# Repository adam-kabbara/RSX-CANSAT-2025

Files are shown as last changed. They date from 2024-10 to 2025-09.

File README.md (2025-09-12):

# RSX CanSat 2T4-2T5 Designs 

<div style="display: flex; gap: 20px; align-items: center;">
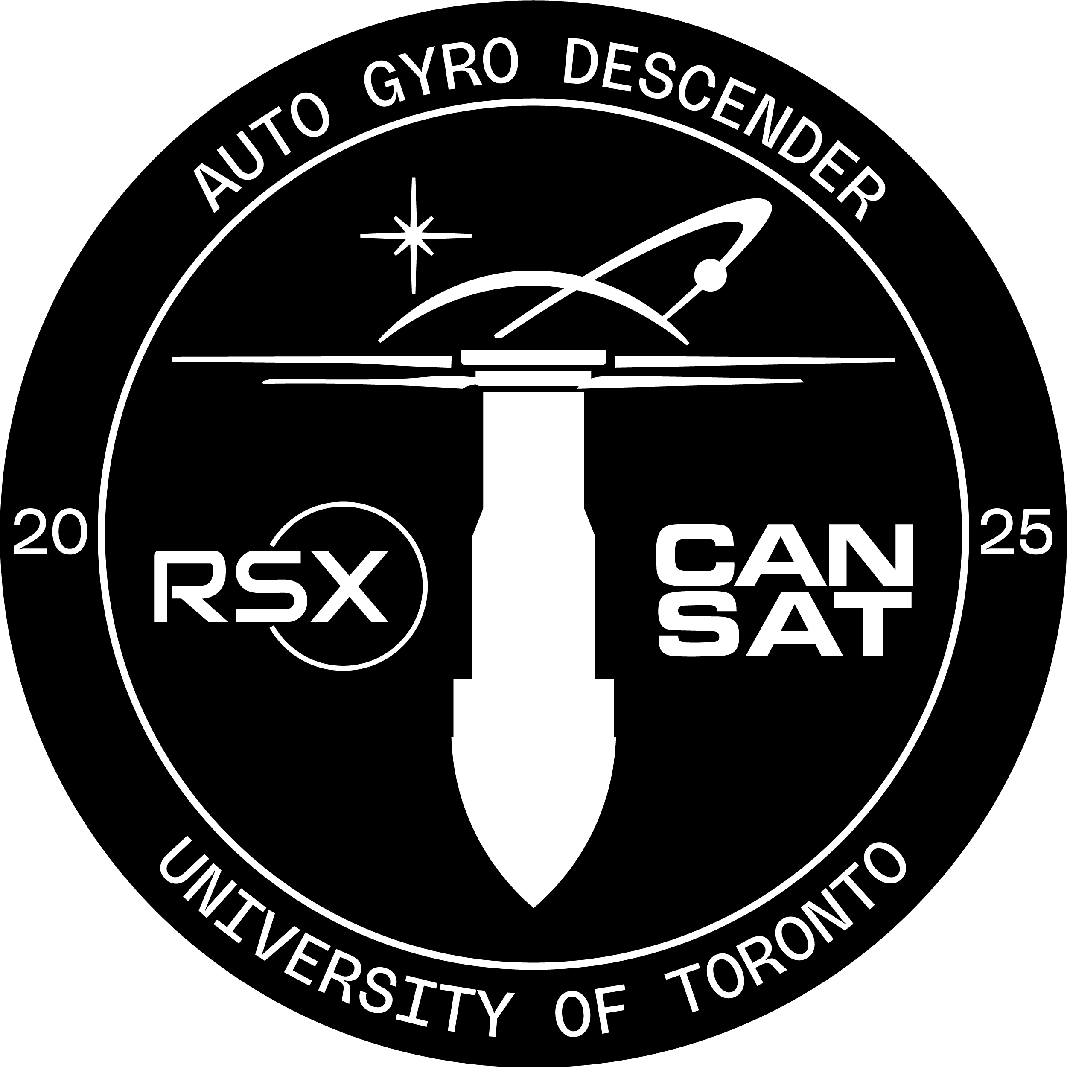
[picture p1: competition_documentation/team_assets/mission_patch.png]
mission_patch
  
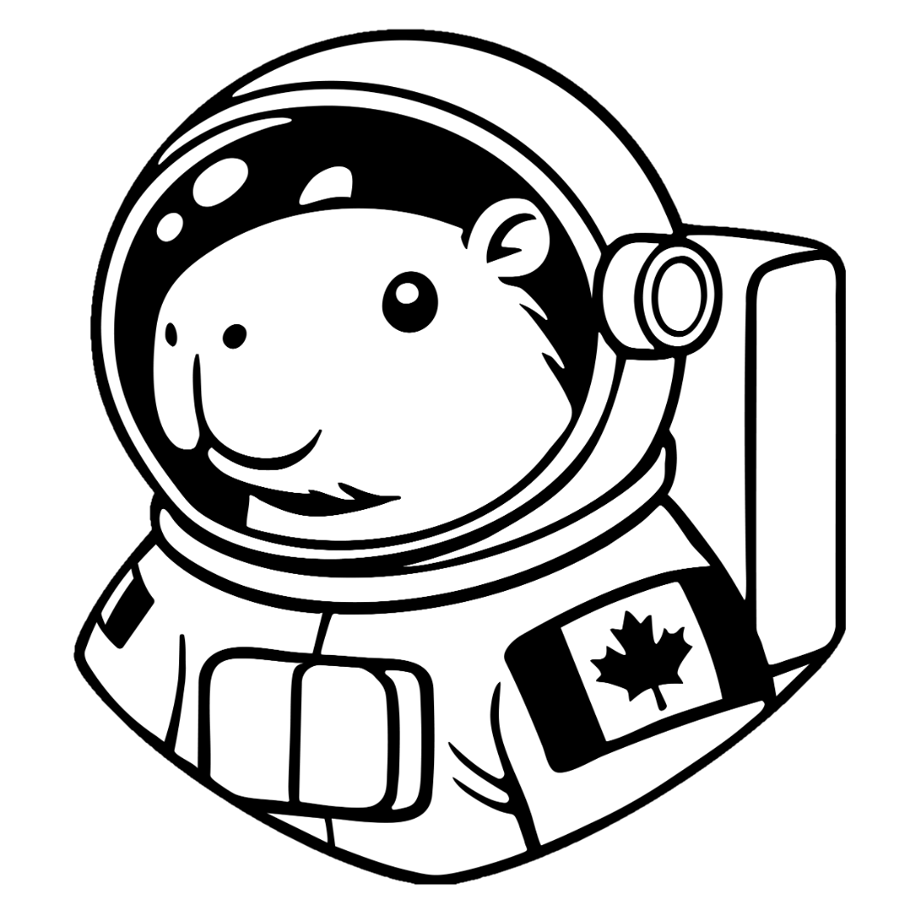
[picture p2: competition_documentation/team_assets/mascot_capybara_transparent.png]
mascot_capybara
  
  uoft_engineering_logo
</div>
<br>

This repository is designed to manage the files made by the CanSat Team under the Robotics for Space eXploration (RSX) design team at the University of Toronto. 

**Competition Team Members:**
- Adam Kabbara | CanSat Team Lead
- Arthur Goetzke-Coburn | Mechanical Team Lead
- Daniel Yu | Electrical Team Lead
- Luke Watson | Software Team Lead
- Gianluca Ceccacci | Mechanical Team Member
- Nour Barsoum | Electrical Team Member
- Angelique Liao | Software Team Member
- Alexey Albert | Mechanical Team Member
- Robert Saab | Electrical Team Member

**CanSat Competition:**
- 📅 June 5-8, 2025
- 📍 Monterey, Virginia, United States
- 📃 [Mission document](CanSat_Mission_Guide_2025e.pdf)

**Competition Deliverables:**
- 🏆 95.87725%: [CanSat 2025 Winners](https://cansatcompetition.com/winners.html)
- 📋 Scoresheet: [TBA]()
- 💾 Mission Data: [Team #3114 Mission Data](competition_documentation/3114_mission_data_cansat_2025.csv.xlsx)
- 📝 Preliminary Design Review: [Team #3114 PDR](competition_documentation/deliverables/Cansat2025_3114_PDR.pdf)
- 🛠️ Critical Design Review: [Team #3114 CDR](competition_documentation/deliverables/Cansat2025_3114_CDR.pdf)
- 🌡️ Environemental Testing Document: [Team #3114 ENV](competition_documentation/deliverables/Cansat2025_3114_Mission_Operations_Manual.pdf)
- 🗂️ Mission Operations Manual: [Team #3114 MOM](competition_documentation/deliverables/Cansat2025_3114_Mission_Operations_Manual.pdf)
- 🛰️ Post Flight Review: [Team #3114 PFR](competition_documentation/deliverables/Cansat2025_3114_PFR.pdf)
- Note: The links above may be outdated.

**Competition Results:**
- 🗺️ 5th Place Internationally!
- 🌎 1st in North America!
- 🍁 1st in Canada!

## Folder Organization

**Calculations:**
<br> Python functions and calculations for sizing inductors and capacitors in a power electronics circuit, including formulas for inductor DC current, ripple current, peak current, and minimum capacitor value, with example calculations and printouts.

**Circuit Design:**
<br>This folder contains all the KiCad printed circuit board (PCB) designs our team has created. It also includes each PCB's related schematic, layout, and gerber files with associated custom KiCad symbols, footprints, and 3D models.

**Competition Documention:**
<br>All deliverables, team logos, and full results from the 2025 CanSat Competition in Monterey, Virginia, USA!

**Full Sensor Setup:**
<br>Initial code used to connect all payload sensor electronics together for testing before integration with full software telemetry.

**Ground Station/Telemetry Source:**
<br>Mission specific operations on payload and ground station.

**PID:**
<br>The code, notebooks, and scripts for developing, testing, and simulating PID control algorithms and sensor integration for the CanSat project.

**PFR Plots:**
<br>Contains Python scripts and output images for generating 2D and 3D plots of CanSat mission and sensor data, including GPS, altitude, and other telemetry visualizations for post-flight review and analysis.

**Sensor Testing:**
<br>All sensors used on our CanSat are tested separately using an ESP32-WROOM-32D Dev Module microcontroller. This folder contains all related information regarding the tests completed on these sensors including past designs, schematics, pin connections, and code.

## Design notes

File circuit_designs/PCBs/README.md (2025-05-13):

# 2025_Competition_Boards
This folder contains a snapshot of all the schematics, boards, and gerber files of the boards taken to the 2025 CanSat Competition.

# Final_Versions
This folder contains the entire KiCad PCB projects of all three boards inclduing improvements made after competition.

# Old_Versions
This folder contains the entire KiCad PCB projects all three boards before technical review. Most of the stitched VIAs are incorrect.

# Power_Management_Prototypes
This folder contains the KiCad projects of initial buzzer and power management board designs. All were later combined into the CanSat_Power_Management_Board.

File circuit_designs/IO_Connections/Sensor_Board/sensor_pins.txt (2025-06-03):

CanSat_Sensor_Board Pin Connections

Format: <Sensor Connection> --> <ESP32 Pins>

SparkFun XBee Explorer (XBee Pro SB3):
DIN     --> GPIO17
DOUT    --> GPIO16
3.3V    --> 3.3V (Power Board)
GND     --> GND

Hall Effect Sensor:
Vout    --> GPIO34
GND     --> GND
VCC     --> 3.3V (Power Board)

Adafruit BME280 (Temp & Pressure):
VIN --> 3.3V (Power Board)
GND --> GND
SCK --> GPIO22
SDI --> GPIO21

BN-220 (GPS):
GND         --> GND
TX (White)  --> RXD1/GPIO9
RX (Green)  --> TXD1/GPIO10
VCC         --> 3.3V (Power Board)

Adafruit LIS3MDL (Magnetometer):
SDA --> GPIO21
SCL --> GPIO22
GND --> GND
VIN --> 3.3V (Power Board)

Adafruit BNO085 (IMU):
VIN --> 3.3V (Power Board)
RST --> GPIO5
CS  --> GPIO15
DI  --> GPIO23
SCL --> GPIO18
SDA --> GPIO19
INT --> GPIO35 & 10k Ohm Pull-Up Resistor --> 3.3V (Power Board)
P0  --> 3.3V (Power Board)
P1  --> 3.3V (Power Board)
GND --> GND

LED (Power Indicator):
(+) --> 10 Ohm Resistor --> 3.3V (Power Board)
(-) --> GND

Servo 1 (Fin 1):
Signal  --> GPIO2
VCC     --> 7.4V (Power Board)
GND     --> GND

Servo 2 (Fin 2):
Signal  --> GPIO4
VCC     --> 7.4V (Power Board)
GND     --> GND

Servo 3 (Camera):
Signal  --> GPIO27
VCC     --> 7.4V (Power Board)
GND     --> GND

Servo 4 (CPL 1):
Signal  --> GPIO14
VCC     --> 7.4V (Power Board)
GND     --> GND

Servo 5 (CPL 2):
Signal  --> GPIO12
VCC     --> 7.4V (Power Board)
GND     --> GND

Servo 6 (CPL 3):
Signal  --> GPIO13
VCC     --> 7.4V (Power Board)
GND     --> GND

Camera Board (JST):
VCC     --> 7.4V (Power Board)
Signal1 --> GPIO32
Signal2 --> GPIO33
Data1   --> GPIO25
Data2   --> GPIO26
GND     --> GND

Power Board (JST):
3.3V
7.4V    --> 5V & Six Servos & Camera Board (JST)
ADC     --> GPIO39
GND

Booster + Battery connections not included here, as well as various resistors and capacitors, please see the schematic for more details here:
/$USER/RSX-CANSAT-2T4-2T5/RSX-CANSAT-2025/circuit_designs/PCBs/CanSat_Sensor_Board/CanSat_Sensor_Board.kicad_sch

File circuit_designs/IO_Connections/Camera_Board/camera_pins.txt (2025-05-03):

CanSat_Camera_Board Pin Connections

Format: <JST Connection> --> <ESP32 Camera Pins>

Acronyms:
PRC = Payload Release Camera (Camera 1)
GC  = Ground Camera (Camera 2)

JST Connection: 
VCC     --> PRC 5V & GC 5V
Signal1 --> PRC GPIO14
Signal2 --> GC GPIO14
Data1   --> PRC GPIO21
Data2   --> GC GPIO21
GND     --> PRC GND & GC GND

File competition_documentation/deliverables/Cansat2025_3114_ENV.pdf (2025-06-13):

### Team Logo Here (If You Want)

# Environmental Test Document

# Team #3114 Robotics for Space eXploration (RSX)

### Here

### (If You Want) Overview

# - Thermal test - Vibration test - Vaccuum test - Drop test

# Even though the vacuumed test was not able to reach the expected apogee of 700m, changing the code to allow apogee to be reached around the maximum vacuumed (~200 m) still displayed how the cansat would eject once it reaches apogee

### Here

# (If You Want) Drop Test Configuration

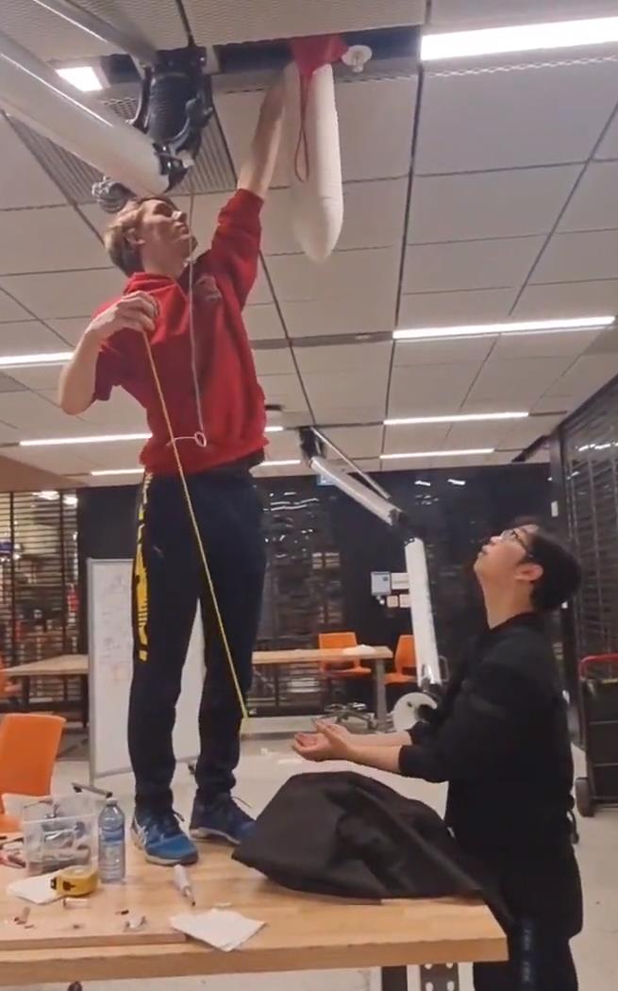
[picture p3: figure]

### Requirements:

### Telemetry must be

received before, during,
and after the drop test.

### Power must not be lost

upon dropping the system.

### Physical components must not detach upon dropping

the CanSat.

### Components of the CanSat should not be damaged from the drop

test.

### The test structure must not

be held by hand.

### Materials:

### 61 cm, 5/8" tubular nylon cord

### Eyebolt

### Scrap wood and Clamps

### Winter Jackets (padding)

Setup:

Two 2x4s are placed on the corner of the balcony above Myhal Arena and a large piece of scrap plywood with an eyebolt screwed into the centre and directed towards the ground is placed on top of the 2x4s. The wood is clamped to the rails of the balcony using 4 clamps. The eyebolt of the testing rig is attached via the nylon cord to a second eyebolt screwed into a plywood disk fed through the hole of the parachute and taped to the parachute to ensure it stays centered. Place winter jackets on the ground below the test fixture to act as a safety net for the CanSat if it drops.

### Here

# (If You Want) Drop Test Procedures

## Procedure:

1) Power on CanSat.
2) Verify telemetry is being received.

## 3) Assemble the testing rig described in the previous

slide.

4) Start video recording this testing procedure.

## 5) Feed the wooden disk with an eyebolt through the

## hole of the parachute. Use tape to keep the eyebolt

in the centre of the hole.

6) Using the tubular nylon, attach these two eyebolts,

a distance of 61cm away from each other.

## 7) Photograph how the CanSat and parachute are

fastened to the testing rig.

## 8) Raise CanSat by the attached cord, so that the

## attachment points of the cord, on the eye bolt and the

parachute, are at the same height.

9) Photograph the CanSat at this point in the procedure.
10) Release the CanSat.
11) Photograph the CanSat after the drop.
12) Verify the CanSat did not lose power.
13) Turn the CanSat off.
14) Inspect for any damage, or detached parts.
15) Verify telemetry is still being received.
16) Stop the video recording.

## 17) Make this video available to the judges and ensure it

does not exceed 5 minutes in length.

### Here

# (If You Want) Drop Test Results

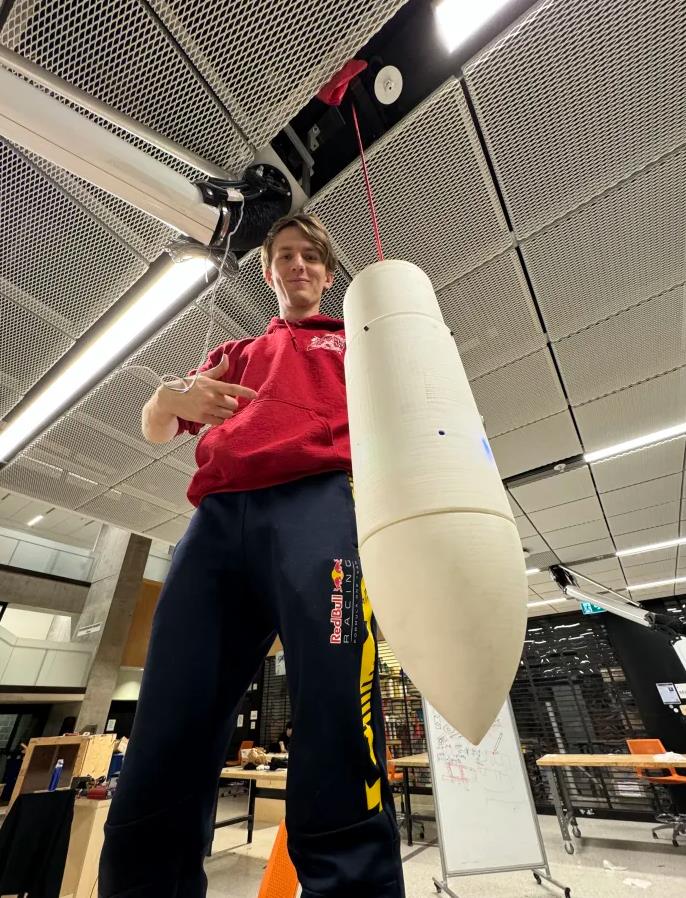
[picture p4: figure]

# Video Link: https://drive.google.com/file/d/1sROrkcR7NDwY3

mso1kv6UxrnZrP9bl7X/view?usp=sharing (https://drive.google.com/file/d/1sROrkcR7NDwY3mso1kv6UxrnZrP9bl7X/view?usp=sharing)

# Result: The cansat was still functioning normally

after the drop test, and it was structurally sound,

# as explain by our mech lead, Arthur in the linked

video.

### Here

# (If You Want) Thermal Test Configuration

### Requirements:

Power must not be lost while heating the system.

### Components of the CanSat should not be damaged from the Thermal

test.

### The rubber bands applying the force to lift the rotor joints shall take the same amount of time to deploy the rotors before and after the thermal

test.

### Materials:

### Thermal Chainber (3D printer with heated bed)

### Heat Gun

### LCD thermometer

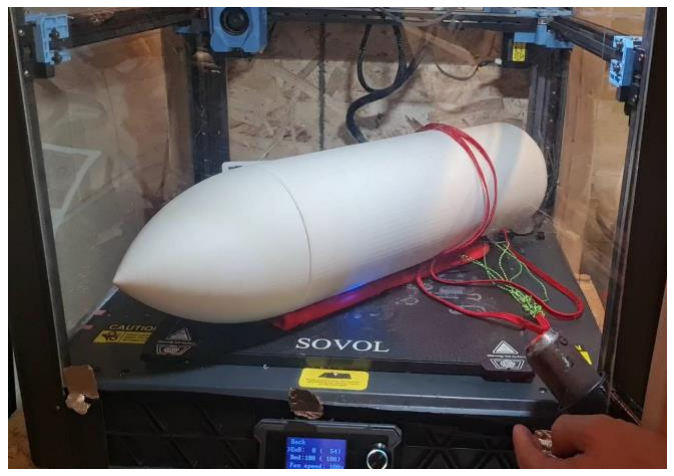
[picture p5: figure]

Setup:

Set up the heated but to 100 degrees C. This makes the thermal chamber reach 60 degrees C. The thermal chamber loses heat due to imperfections in the chamber. We use

Before putting the cansat in the chamber, put a thermally insulating layer to avoid the cansat direct contact with the 100-degree bed.

### Here

# (If You Want) Thermal Test Procedures

Procedure:

1) Using a Newton Force Meter Spring Scale,

measure the force required to lift a single air

foil. Video this process.

2) Clamp one end of the fin down along a

distance of 2cms down the fin. Place the mass

at the opposite end, and using two rulers,

measure the8) Raise CanSat by the attached

cord, so that the attachment points of the cord,

on the eye bolt and the parachute, are at the

same height. distance that the system bends

downward. Video tape this process.

3) Place CanSat into a thermal chamber in a

secure fashion and video this process.

4) Photograph the manner in which the CanSat

is secured.

5) Turn on the CanSat.
6) Close and seal the thermal chamber.
7) Turn on the heat source.
8) Monitor the temperature and turn off the heat

source when the internal temperature reaches

60C and turn on the heat source when the

temperature drops to 55C.

9) Take a short video highlighting abidence to

the above step.

10) Maintain the test conditions for two hours.
11) Turn off the heat source and perform visual

inspection and any functional tests to verify the

Cansat survived the thermal exposure and can

operate as expected. Ensure there is no visible

warping or any broken or loose components.

12) Photograph the system.
13) Start a video recording.
14) With the CanSat still hot, remove the

CanSat from the chamber.

15) Test any mechanisms and structures to

ensure the integrity has not been compromised.

Force deployment and ensure the AGDS does

not get stuck within the CC due to thermal

expansion.

16) Verify through telemetry that the electronics

are consistently functional.

17) Turn off the CanSat.
18) Verify epoxy joints and composite materials

still maintain their strengths by repeating steps

1) and 2).
19) Stop the video recording
20) Splice together the many short videos into

one long video. Ensure this video is less than 5

minutes long.

21) Make this video available to the judges.

### Here

# (If You Want) Thermal Test Procedures

Procedure:

1) Test the CanSat motor release system is

valid. Video tape this process.

2) Place a thermometer inside of the thermal

chamber. Place a glove on the layer of the

thermal chamber avoid CanSat's direct

attachment to the heat bed. Video tape this

process.

3) Place CanSat into a thermal chamber in a

secure fashion and video this process.

4) Photograph the manner in which the CanSat

is secured.

5) Tap the sides of the thermal chamber

container and make sure it is properly sealed.

6) Double check if the thermal chamber is

properly sealed.

7) Turn on the heat source.
8) Monitor the temperature and turn off the heat

source when the internal temperature reaches

60C and turn on the heat source when the

temperature drops to 55C.

9) Take a short video highlighting abidence to

the above step.

10) Maintain the test conditions for two hours.
11) Turn off the heat source and perform visual

inspection and any functional tests to verify the

Cansat survived the thermal exposure and can

operate as expected. Ensure there is no visible

warping or any broken or loose components.

12) Photograph the system.
13) Start a video recording.
14) With the CanSat still hot, remove the

CanSat from the chamber.

15) Test any mechanisms and structures to

ensure the integrity has not been compromised.

Force deployment and ensure the AGDS does

not get stuck within the CC due to thermal

expansion.

16) Verify through telemetry that the electronics

are consistently functional.

17) Turn off the CanSat.
18) Verify epoxy joints and composite materials

still maintain their strengths by repeating steps

### Here

# (If You Want) Thermal Test Results

# Video link: https://drive.google.com/file/d/1xN-CH3U1Kcelx69eaLlpqZKlPzbh1Y-

5/view?usp=drive_link (https://drive.google.com/file/d/1xN-CH3U1Kcelx69eaLlpqZKlPzbh1Y-5/view?usp=drive_link)

# Result shows that the rotor deployment has not been affected by high

temperature around 60 degrees.

### Here

# (If You Want) Vibration Test Configuration

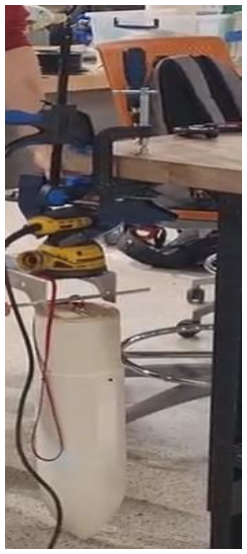
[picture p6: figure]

### Requirements:

### Accelerometer data must continue to be recorded and sent throughout the

entirety of the testing procedure.

### The CanSat must be able to withstand the vibrational shock without physical

damage.

### The Random Orbital Sander must not

be held by hand.

Materials:

Random Orbital Sander (GIVE MODEL NUMBER)

Bench Vise

Plywood, Metal Brackets, Screws to fasten, Bolt, Washer, and Nut

Double sided Tape

Setup:

The orbital sander will be secured, downward facing, in the vise bench. A plywood disk the size of the sander's face will be attached using strong double-sided tape to the sander itself. This disk will have two small metal brackets screwed into it, spaced the width of the CC's eyebolt, enabling a bolt to pass through them and the eye bolt of the CC. A washer and nut will be tightened, creating pressure between the two brackets and the eyebolt.

### Here

# (If You Want) Vibration Test Procedures

## Procedure:

1) Power on the CanSat.
2) Verify accelerometer data is being collected.

### 3) Take a photograph of this setup. Take additional

### photos highlighting how the CanSat was secured

explained in the setup on the previous slide.

4) Start a video recording.
5) Power up the sander.

### 6) Once the sander is up to full speed, wait 5

seconds.

7) Power down the sander to a full stop.
8) Repeat steps 5) to 7) four more times.
9) Photograph the CanSat.
10) Inspect the CanSat for damage and functionality.
11) Verify accelerometer data is still being collected.

### 12) Stop the video recording and ensure it is under 5

### minutes in length. Make this video available to the

judges.

13) Power down CanSat.

### Here

# (If You Want) Vibration Test Results

# - Results show that the cansat is still function and transmitting data after being

subjected to 20 to 29 G of vibrations.

# - Video Link: https://drive.google.com/file/d/1s6XSHnLbIq4v2N4K2l2q6ZPo6ZZZhTwv/view

?usp=drive_link (https://drive.google.com/file/d/1s6XSHnLbIq4v2N4K2l2q6ZPo6ZZZhTwv/view?usp=drive_link)

- Note: The magnetometer readings are showing 0 Gauss due to the small magnetic fields likely

## in the decimals and our GUI does not specify further than one full unit

- Note: The accelerometer readings are only showing up to +-4G due to the original settings of the BNO-085 IMU sensor, however, our orbital saner is creating up to +-25G.

### Here

# (If You Want) Vacuum Test Configuration

### Requirements:

Telemetry must be received before, during, and after the vacuum test.

Telemetry must be exportable as a .csv.

### The CanSat must decouple based off the simulated altitude data at 75%

of the simulated apogee.

### Materials: IKEA 12-gallon bin

### Vacuum

### Gray Duct Tape

### Clear garbage bag

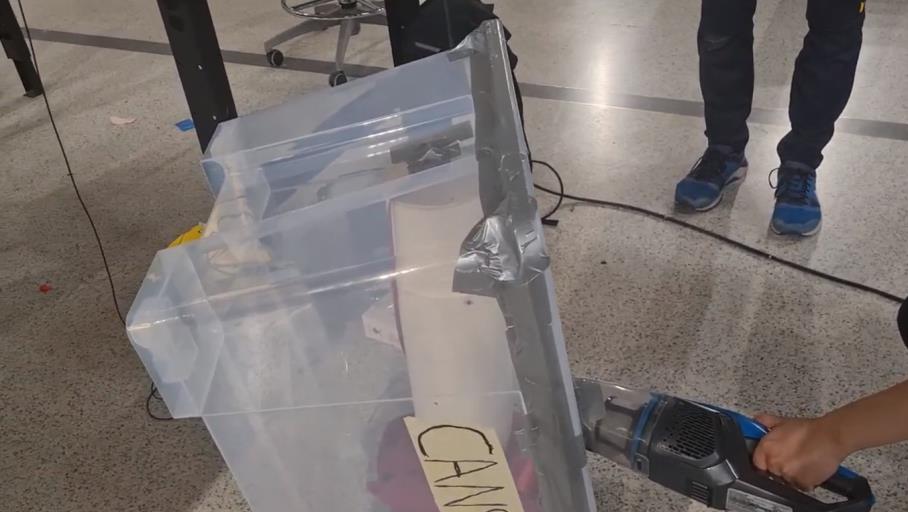
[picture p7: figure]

Setup:

Using the CanSat Container's eyebolt, the system is to be taped to the bin. A towel is placed below the suspended system for padding. A garbage bag was pulled tight over the open side of the bin where the lid would go, and the bag is taped to the bin using the sealant tape. A small hole is cut into the bag and it is pulled over the nozzle of the vacuum. The edges of this tear are taped to the vacuum in order to create an airtight chamber.

### Here

# (If You Want) Vacuum Test Procedures

## Procedure:

1) Start a video recording.

### 2) Suspend the fully configured and powered CanSat in

### the vacuum chamber in the manner described in the

setup on the previous slide.

3) Take a photograph of this setup.
4) Turn on the vacuum to start generating suction.

### 5) Monitor the telemetry in simulation mode and stop the

vacuum when the peak altitude has been reached.

### 6) Let the air enter the vacuum chamber slowly and

### monitor the operation of the CanSat. The air will leak

through the vacuum cleaner when off.

### 7) Ensure the AGDS decouples from the CC at 75%

apogee.

### 8) Stop the video and ensure it shows all mechanisms

activated based on altitude changes.

9) Collect the CanSat from the vacuum chamber.
10) Collect and save the telemetry.
11) Power off the CanSat.

### 12) Make the saved telemetry available for the judges to

review.

### 13) Ensure the video is under 5 minutes long and make

it available to the judges.

### Here

# (If You Want) Vacuum Test Results

# - Video link: https://drive.google.com/file/d/1sOdRuyu7-

IHa7KviOOJac89K6n2n80d5/view?usp=sharing (https://drive.google.com/file/d/1sOdRuyu7-IHa7KviOOJac89K6n2n80d5/view?usp=sharing%E2%80%83)

# - The vacuum test was a success even though the pressure in the enclosure did not reach the expected apogee pressure – the finite state machine was able to be performed as the "Apogee" state was reached when the pressure

became constant for a few seconds after rising over a specific threshold.

### Here

### (If You Want) Summary

# - The tests were a success - For next year, it would be nice to have a more powerful vacuume that allows us to simulate lower pressures similar to that which the cansat will experience at apogee (~700)

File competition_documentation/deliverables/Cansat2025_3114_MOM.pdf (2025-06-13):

# Mission Operations Manual (Check List) Team 3114 (RSX) Version 2.0

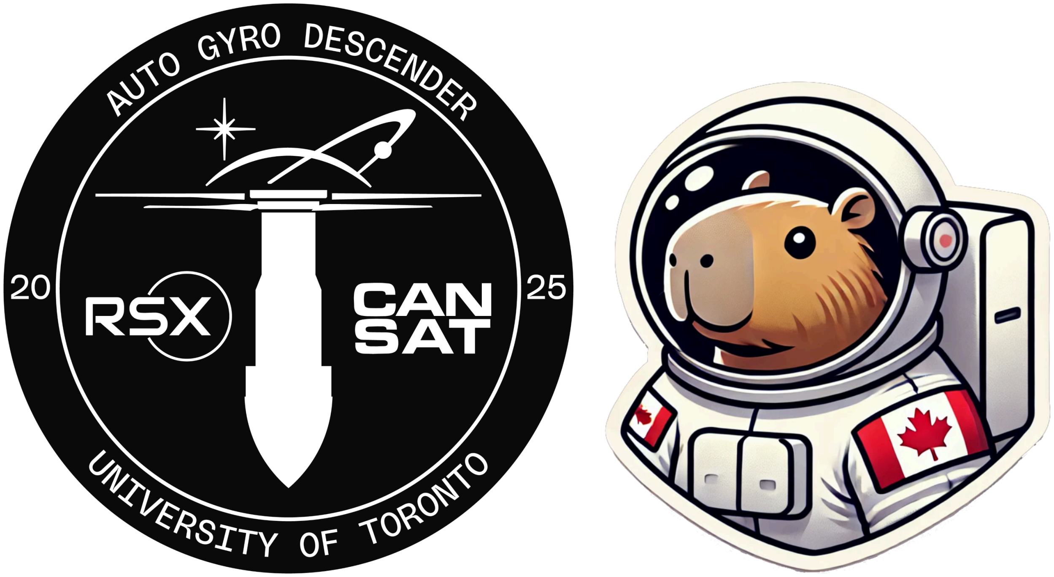
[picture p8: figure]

Ground Station Configuration | 2
Cansat Preparation | 3
Cansat Integration | 4
Launch Preparation | 4
Launch Procedures | 4

Ground Station Configuration
Ground Station Crew (GSC): Luke Watson and Angelique Liao

Ground station crew heads to ground station tables to set up the ground station.
Connect the RPSMA wire from the QHA antenna into the ground station XBee.
Insert the ground station XBee into the SparkFun XBee regulated dongle and connect to the ground station laptop to provide power through the USB port of the ground station laptop.
Place the antenna on the table using the stand and prepare for use as a handheld antenna right before launch.
Turn on the ground station laptop, run the ground station GUI, and select the correct serial (COM) XBee under the connection tab.
Ensure that the Net ID on the XBee is set to the Team ID and change if necessary.
After the Cansat is powered on, check the connection with the ground station under the connection tab to ensure everything is set up correctly. From the GUI, send the altitude calibration command to zero the barometer. Also ensure to set the time as well to either GPS time or ground station computer time depending on the judges’ input. Verify updated values in the telemetry Live Values section.
Finally, to start the mission and telemetry graphing, click Start Mission under the Telemetry tab.

Cansat Preparation
CanSat Crew (CCR): Arthur Goetkze-Coburn, Alexey Albert, Daniel Yu

On the Cansat Payload, open one half of the shroud to verify both Cansat batteries (main and buzzer) are fully charged (~8.4v and 4.2v respectively) and securely connected. Double check the RTC backup battery voltage as well and replace it if the voltage is lower than 3v.
Disconnect the main board from both the power and camera board. Upload the last stable version of the flight software to the main ESP32. Ensure both camera ESP32s have SD cards. Blue SD card belongs to camera 1 (ESP32 closer to JST) and red SD card belongs to camera 2. To access SD card on camera 2, undo the camera cable extension. Reconnect all three boards together, turn on both main and buzzer switches, and ensure that all three boards all light up.
Confirm that the ground station GUI is able to receive telemetry data and is able to detect the ground camera boards after the completion of the Ground Station Configuration operation.
Debug any problems that arise, then put the second half of the shroud back onto the Cansat Payload.
Ensure all the rubber bands on the rotors are attached correctly and replace them if they are broken.
Actuate all four rotors. Both GYRO servos should be at rest (parallel to the shroud direction) at 90 degrees. The Camera servo should also be at rest at 90 degrees (pointing in the normal direction of the Cansat shroud). The rest position of the Release servo is at 0 degrees (holding the payload) Actuate both GYRO servos to 135 (+45 rel) and 45 (-45 rel) Actuate the Camera servo to 100 (+10 rel) and 80 (-10 rel)
Actuate the Release servo to 35 (+35 from rel) and back to 0.
Turn off the Cansat.
Separate the Cansat container from its shoulder. Fold the rotors down and place the Cansat payload into the Cansat container’s wall.
Slide the top rotor shaft into the container's shoulder
Turn the ESP32 back on, this will initiate the container integration sequence which will move the release servo out of the way, allowing the payload’s rotor shaft to slide in, and then actuates 10 seconds later to lock the payload in place.
Turn off the Cansat to save battery and wait for the Integration step.

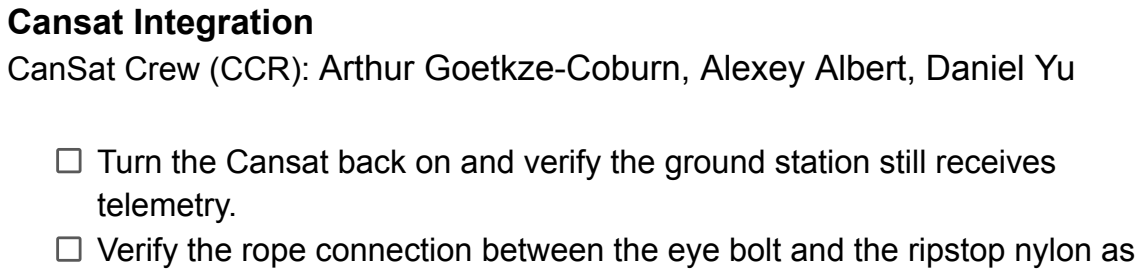
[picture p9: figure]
Cansat Integration; telemetry.

CanSat Crew (CCR): Arthur Goetkze-Coburn, Alexey Albert, Daniel Yu

Turn the Cansat back on and verify the ground station still receives

Verify the rope connection between the eye bolt and the ripstop nylon as well as the connection between the ripstop nylon rope and the 6 parachute ropes.
Fold the parachute and put it in the rocket payload section before the Cansat. Insert the Cansat container into the rocket payload section with the eyebolt going in first and the nose cone pointing to the sky.

Launch Preparation

Take the rocket to the flight line and get a launch pad assignment (should be pad #3 if no changes have been made according to the preflight brief). Walk out with the pad manager and have the rocket installed on the rail. Pad manager installs igniter.
Pad manager verifies igniter continuity if launcher has continuity tester. Team takes a picture next to the rocket.
Team goes back to the flight line and is assigned crew positions.

Launch Procedures
Mission control officer will step through this procedure to launch the Cansat. At any time during the launch procedure, any crew member or officer can call out for a hold to stop the launch. It is required to say HOLD three times using a voice radio to stop the launch. If the hold does not require the rocket to be removed from the launch pad, then the procedures are stopped at the current step. If the hold requires the Cansat to be removed, the removal procedures must be executed.

Flight coordinator will query field judges and spotters if they are ready for the next launch.
Mission Control Officer (Adam) performs any pre-launch checks.
The Mission Control Officer (Adam) will verify with the ground station that the ground station is ready for launch.

Mission Control Officer (Adam) will request Launch Control Officer to select appropriate launch pad.
The Mission Control Officer (Adam) will tell the Launch Control Officer when to launch the rocket.
The Launch Control Officer will launch the rocket.

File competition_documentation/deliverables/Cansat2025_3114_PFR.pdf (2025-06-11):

CanSat 2025 PFR: Team #3114 | RSX | 1

# CanSat 2025 Post Flight Review (PFR) Outline

## Team #3114 Robotics for Space eXploration (UofT)

## Presentation Outline

Presenter: Adam Kabbara

Section | Presenter | Slides
Systems Overview | Arthur Goetzke-Coburn, Gianluca Ceccaci | 4-7
Concept of Operations and Sequence of Events | Alexey Albert, Angelique Liao | 8-11
Flight Data Analysis | Luke Watson, Daniel Yu, Alexey Albert | 12-26
Failure Analysis | Adam Kabbara | 27-29
Lessons Learned | Arthur Goetzke-Coburn, Gianluca Ceccacci | 30-31
Conclusion | Adam Kabbara | 32

## Team Organization

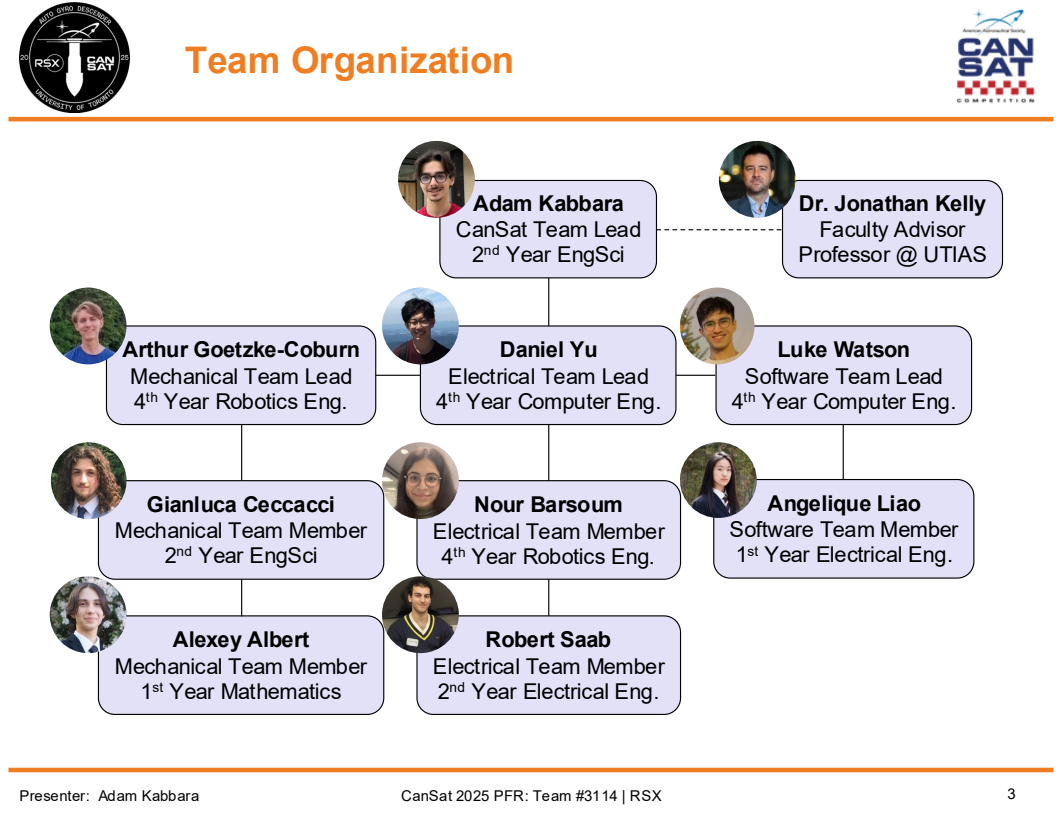
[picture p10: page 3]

Adam Kabbara
CanSat Team Lead
nd Year EngSci

Dr. Jonathan Kelly
Faculty Advisor
Professor @ UTIAS

Arthur Goetzke-Coburn
Mechanical Team Lead
th Year Robotics Eng.

Daniel Yu
Electrical Team Lead
th Year Computer Eng.

Luke Watson
Software Team Lead

Angelique Liao
Software Team Member
st Year Electrical Eng.

Gianluca Ceccacci
Mechanical Team Member

Nour Barsoum
Electrical Team Member

Alexey Albert
st Year Mathematics

Robert Saab
nd Year Electrical Eng.

Presenter: Adam Kabbara

# Systems Overview

## Arthur Goetzke-Coburn & Gianluca Ceccacci

## Payload Design Description (1/2)

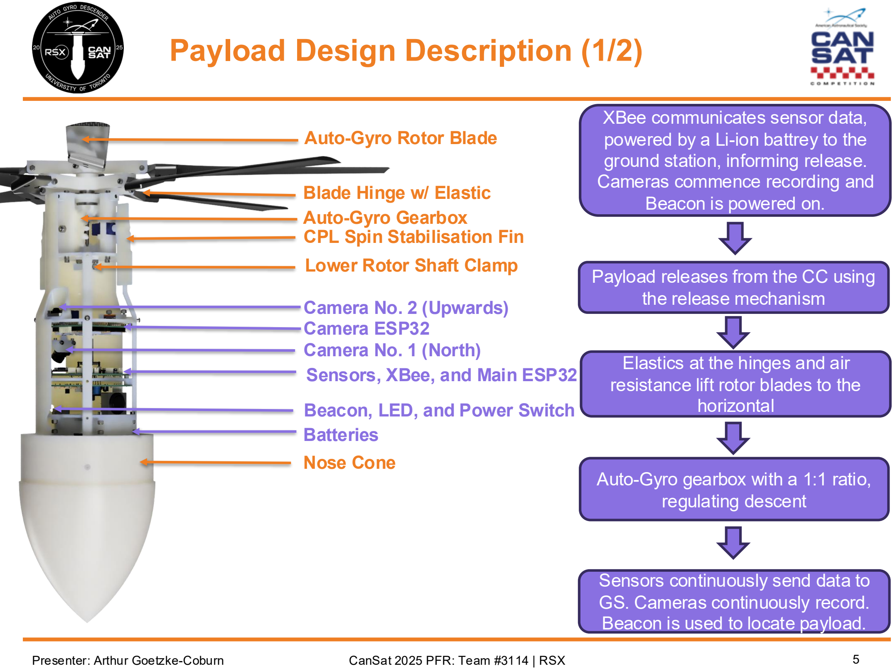
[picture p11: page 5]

Presenter: Arthur Goetzke-Coburn

Nose Cone

Batteries

Sensors, XBee, and Main ESP32

Camera No. 1 (North)

Camera No. 2 (Upwards)

CPL Spin Stabilisation Fin

Auto-Gyro Gearbox

Lower Rotor Shaft Clamp

Auto-Gyro Rotor Blade

Blade Hinge w/ Elastic

Beacon, LED, and Power Switch

Camera ESP32

Payload releases from the CC using the release mechanism

Elastics at the hinges and air resistance lift rotor blades to the horizontal

Auto-Gyro gearbox with a 1:1 ratio, regulating descent

XBee communicates sensor data, powered by a Li-ion battrey to the ground station, informing release. Cameras commence recording and Beacon is powered on.

Sensors continuously send data to GS. Cameras continuously record. Beacon is used to locate payload.

## Payload Design Description (2/2)

Presenter: Arthur Goetzke-Coburn

Type | Air Pressure and Temperature | Battery Voltage | GPS | Hall Effect | IMU | Magnetometer | Camera 1 (Release) | Camera 2 (Ground)
Model | BME280 | ESP32 ADC Pin | NEO-6M | A3144EU | BNO085 | LIS3MDL | OV5640AF | OV5640

Power Management Board

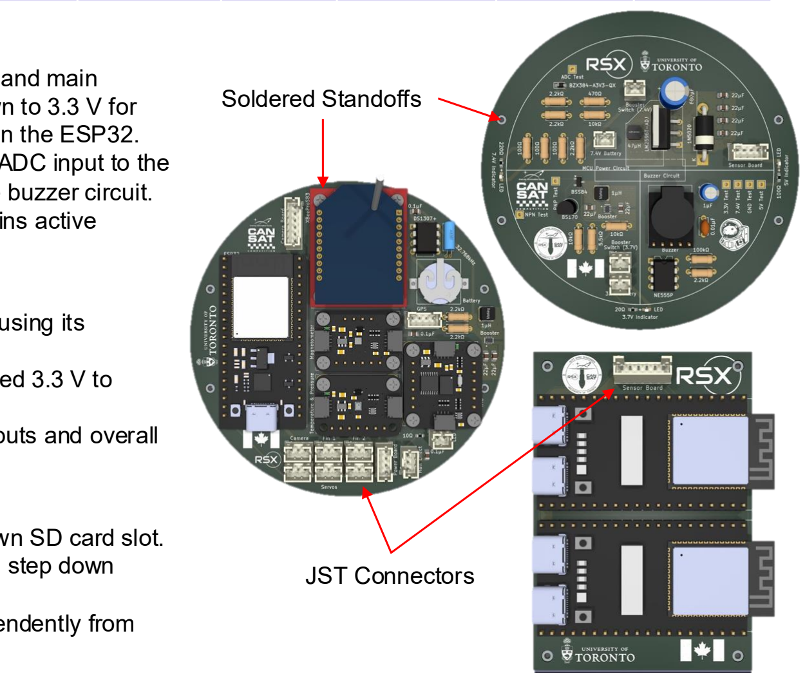
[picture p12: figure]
Soldered Standoffs; JST Connectors

- Distributes 7.4 V from the battery to the camera and main
boards, powers servos directly, and steps it down to 3.3 V for XBee and high-current sensors to reduce load on the ESP32.
- Converts 7.4 V to 3.3 V via a voltage divider for ADC input to the ESP32, and boosts a 3.7 V battery to 5 V for the buzzer circuit.
- Includes a self-sustaining timer circuit that remains active across system restarts.

Main Board
- Hosts an ESP32 that steps down 7.4 V to 3.3 V using its onboard buck converter.
- Powers digital sensors with the ESP32’s regulated 3.3 V to ensure clean and stable signals.
- Central controller for managing digital sensor inputs and overall system control.

Camera Board
- Contains two ESP32s, each equipped with its own SD card slot.
- Each ESP32 uses its onboard buck converter to step down 7.4 V to 3.3 V for stable camera operation.
- Handles camera control and data logging independently from the main board.

## Container Design Description

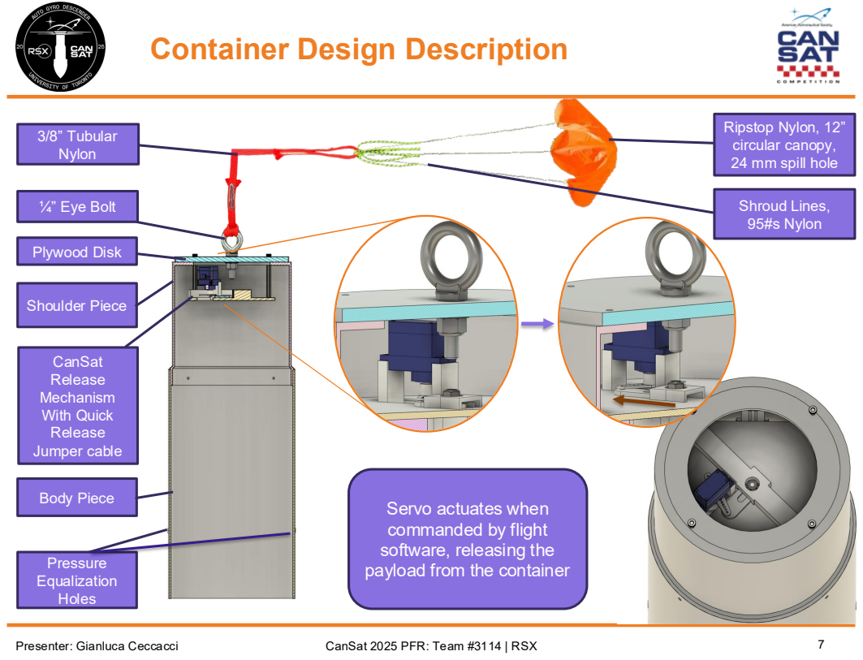
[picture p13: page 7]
Pressure Equalization Holes; ¼” Eye Bolt; Plywood Disk; CanSat Release Mechanism With Quick Release Jumper cable; Shoulder Piece; Body Piece; Shroud Lines, 95#s Nylon; 3/8” Tubular Nylon

Ripstop Nylon, 12”
circular canopy,
24 mm spill hole

Servo actuates when
commanded by flight
software, releasing the
payload from the container

Presenter: Gianluca Ceccacci

# Concept of Operations and Sequence of Events

## Alexey Albert & Angelique Liao

## Comparison of Planned and Actual CONOPS

Presenter: Alexey Albert

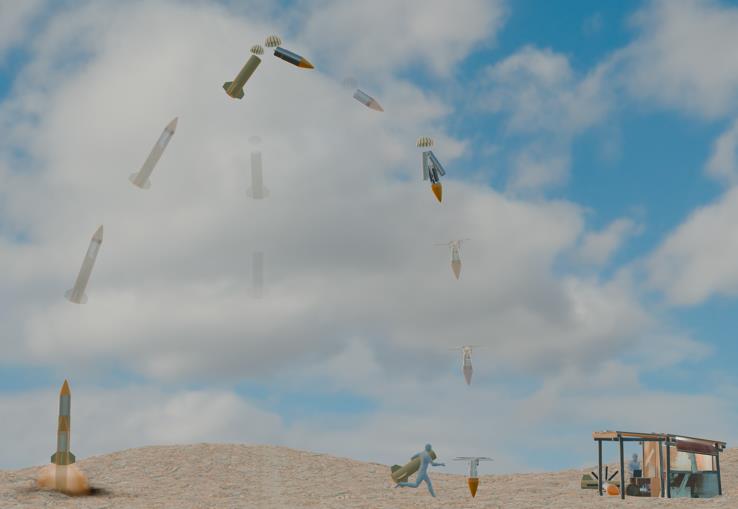
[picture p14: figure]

Pre-launch | Launch | Post-launch
Set up the ground station, including the GUI and the hand-held communication antenna. | Rocket launch while still transmitting telemetry and recording video. | The recovery team scouts for the CanSat using the last known GPS coordinates and the buzzer sound.
Switch on the CanSat (CPL) and the buzzer. | Apogee is reached around ~740 m (assuming J425 engine). CC is deployed and descends with its parachute. Rocket descends and lands with its own parachute.
Ensure XBee enters running as intended. | | The telemetry data received by the GS and the on board CanSat footage are retrieved
Instruct CanSat crew to integrate the CanSat into the rocket. | At 75% apogee (~555 m) CC will deploy the CPL which will descend using the auto-gyro system while CC continues to decent and land with its parachute. | A thumb drive with the telemetry data is prepared and presented to the GS judges.

Calibrate and zero the
onboard flight system
values, including
barometric altitude and roll-pitch-yaw IMU values.

CanSat continuously
collects and sends
telemetry data at 1 Hz.

CPL lands and telemetry
data streaming and video
footage are stopped while
the buzzer keeps beeping.

PFR (includes flight
footage) preparation and
CanSat starts recording | presentation.
and storing video footage
from both cameras.
1. CC is released but does not descend using parachute.
2. All telemetry is transmitted but not all sensors sent valid data.
3. The cameras stopped working mid mission due to over heating.

## Comparison of Planned and Actual SOE (1/2)

Presenter: Angelique Liao

1. Arrival, Ground Station, and Antenna Setup | 2. CanSat Assembly and System Validation | 3. Pre-Launch Checklist
Arriving at the launching site | Battery Charge Level Check | Positioning Ground Control Station
Check and fix any potential damage could happened in the transportation | CanSat Assembly Final Integration and System Check | CanSat Integration Check
Ground Control System Assembly | Communication and Sensor Functionality Check | CanSat + GCS Communication Verification
Antenna Assembly | Weight & Size Compliance Verification | Sensor Calibration: Adjust and verify sensor accuracy and turn on cameras
| Final Inspection Submission | Final Safety Inspection
4. Launch Execution | 5. Post-Landing Recovery | 6. Post-Landing Evaluation and Cleanup
Initiating Launch Procedures | Deploy team to locate and recover the CanSat | Return to check-in for final assessment
Monitor CanSat during flight | Retrieve the onboard storage device MicroSD | Clear the Ground Station area
CanSat Recovery after landing | Flight data backup after recovery | Process and interpret collected flight data

Submit flight data via USB stick to the judge

## Comparison of Planned and Actual SOE (2/2)

Presenter: Angelique Liao

Role | Members | Responsibilities | Events
Mission Control Officer (MCO) | Adam Kabbara | Oversees countdown and readiness. | Launch Check & Control
Ground Station Crew (GSC) | Luke Watson, Angelique Liao, and (Nour Barsoum) Arthur Goetzke-Coburn | Monitors telemetry and commands. | Ground Station Configuration
Recovery Crew (RC) | Gianluca Ceccacci, (Robert Saab) Daniel Yu, and Alexy Albert | Tracks and retrieves CanSat | Post-Landing Recovery
CanSat Crew (CCR) | Arthur Goetzke-Coburn, Alexy Albert, Daniel Yu | CanSat preparation and rocket integration team | CanSat Preparation & CanSat Integration

Two of our members could not make it to launch day so the roles had to be moved around.

# Flight Data Analysis

## Luke Watson, Daniel Yu, & Alexey Albert

## Payload Altitude Plot

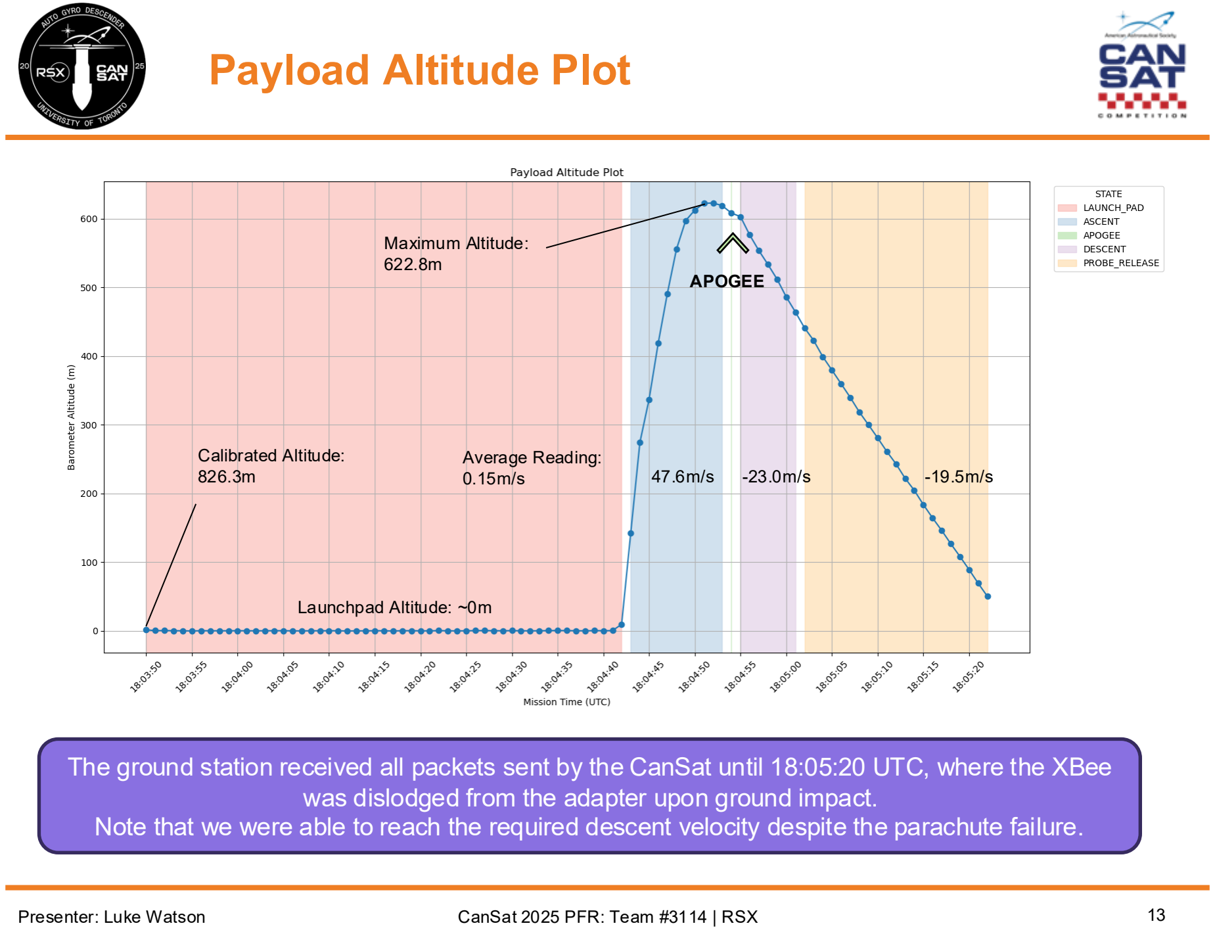
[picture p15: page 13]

Presenter: Luke Watson

The ground station received all packets sent by the CanSat until 18:05:20 UTC, where the XBee was dislodged from the adapter upon ground impact. Note that we were able to reach the required descent velocity despite the parachute failure.

Average Reading:
0.15m/s | 47.6m/s | -23.0m/s | -19.5m/s

Maximum Altitude:
622.8m

Calibrated Altitude:
826.3m

APOGEE

Launchpad Altitude: ~0m

## Probe Release at 75% (1/2)

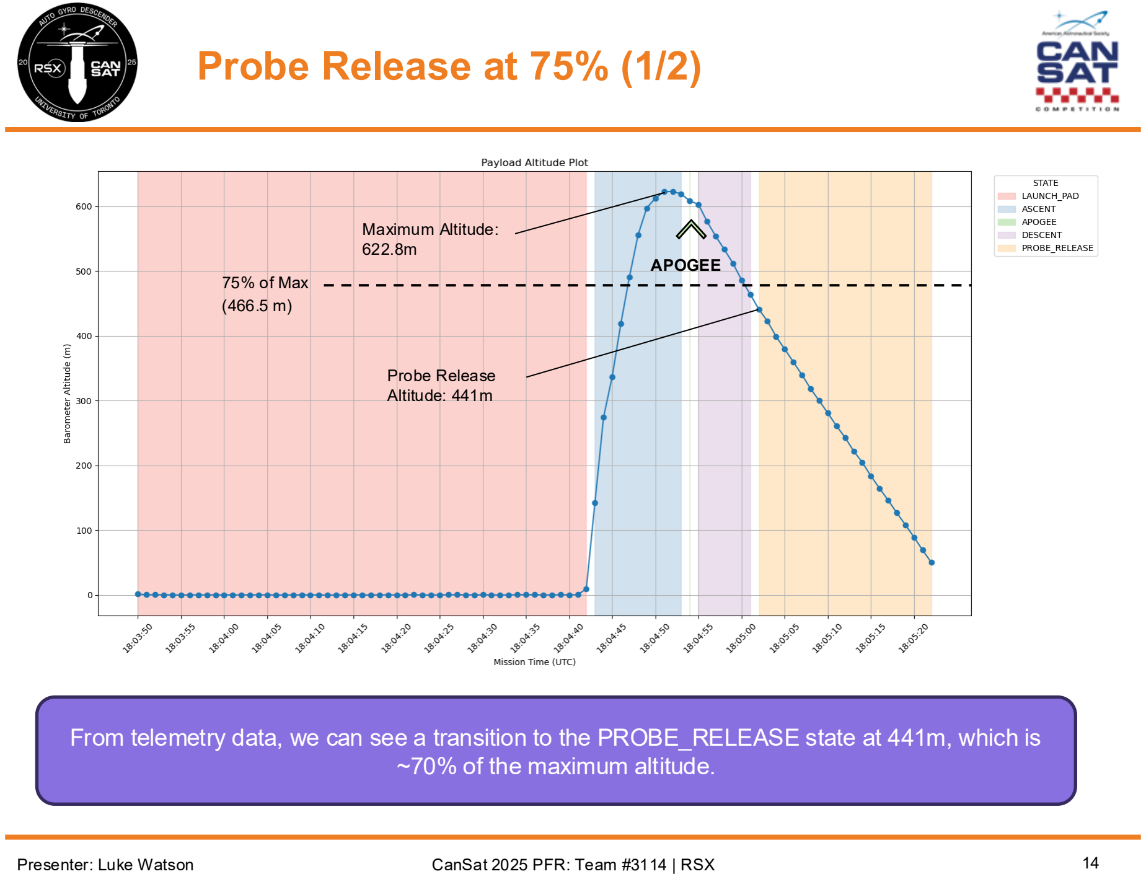
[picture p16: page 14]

Presenter: Luke Watson | CanSat 2025 PFR: Team #3114 | RSX | 14

From telemetry data, we can see a transition to the PROBE_RELEASE state at 441m, which is ~70% of the maximum altitude.

Maximum Altitude:
622.8m

Probe Release
Altitude: 441m

75% of Max

APOGEE

(466.5 m)

## Probe Release at 75% (2/2)

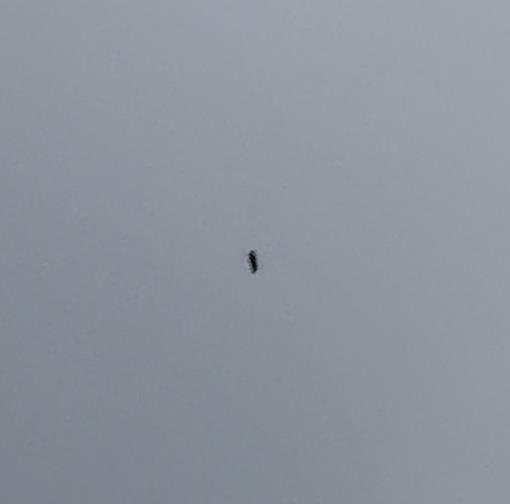
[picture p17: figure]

Presenter: Luke Watson

The FSW was able to successfully separate the payload and container at this time, as shown below:

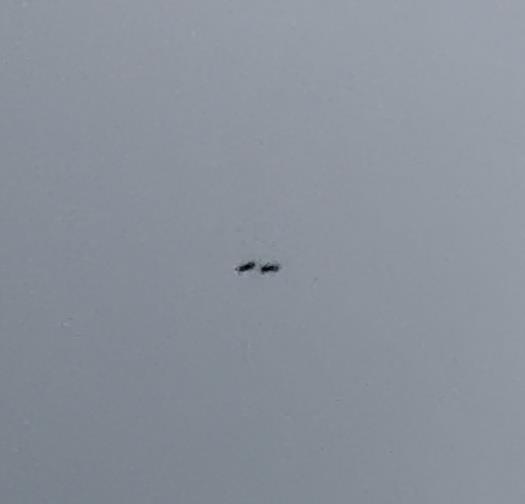
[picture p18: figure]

## Auto-Gyro Descent Rate at 5 m/s

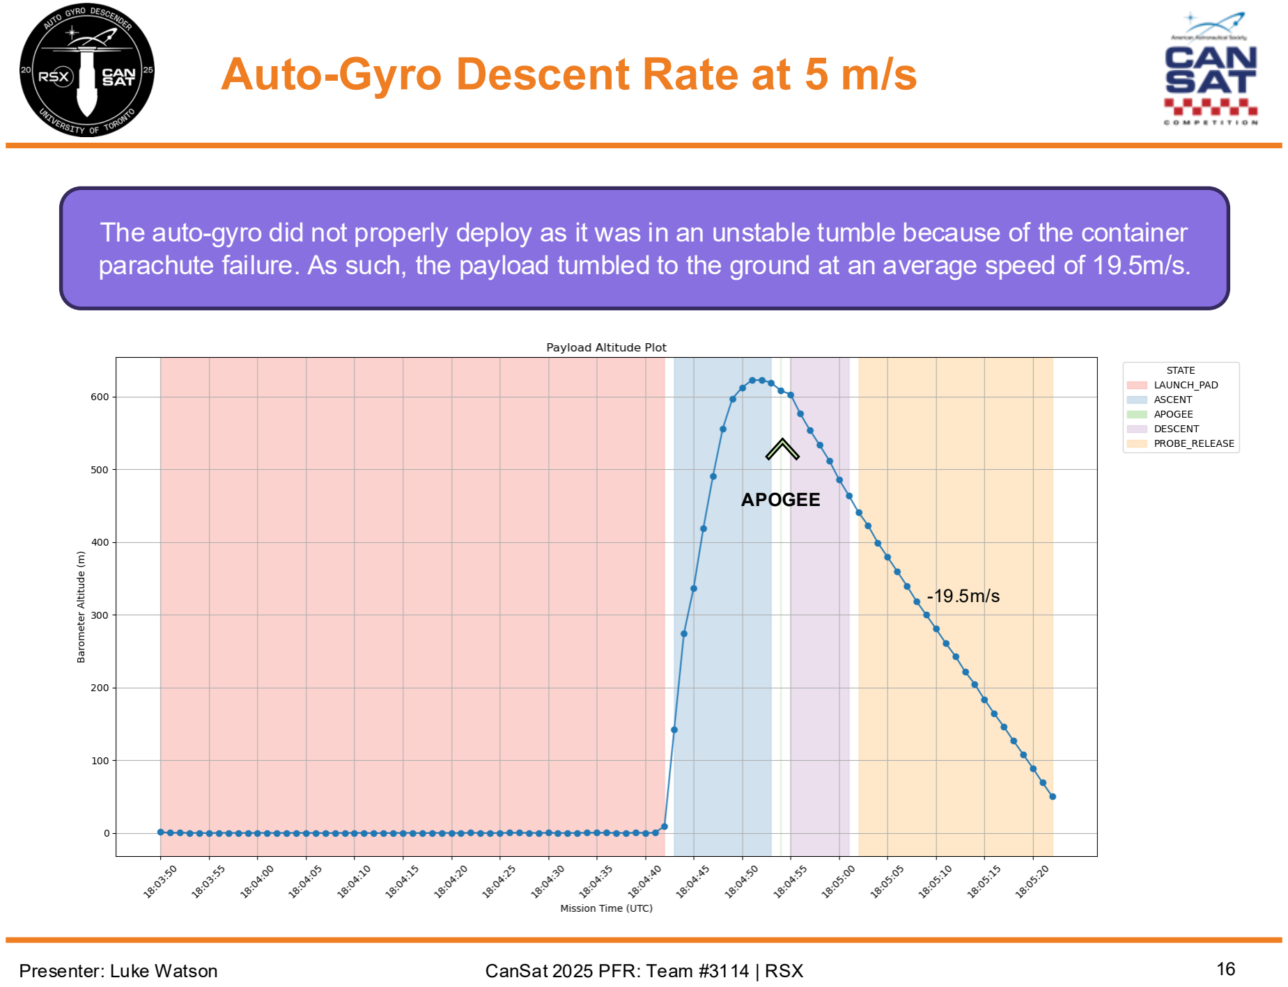
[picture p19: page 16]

Presenter: Luke Watson

The auto-gyro did not properly deploy as it was in an unstable tumble because of the container parachute failure. As such, the payload tumbled to the ground at an average speed of 19.5m/s.

APOGEE

-19.5m/s

## Payload Temperature Sensor Plot

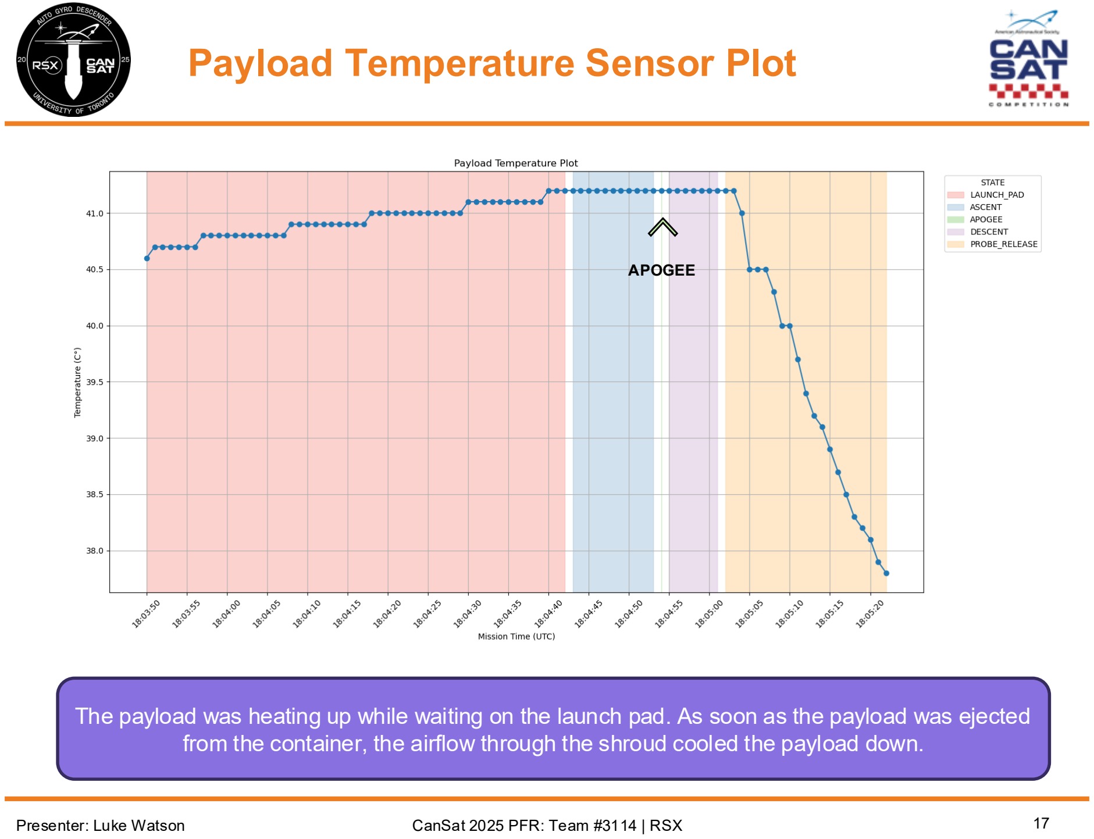
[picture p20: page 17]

Presenter: Luke Watson

The payload was heating up while waiting on the launch pad. As soon as the payload was ejected from the container, the airflow through the shroud cooled the payload down.

APOGEE

## Payload Battery Voltage Plot

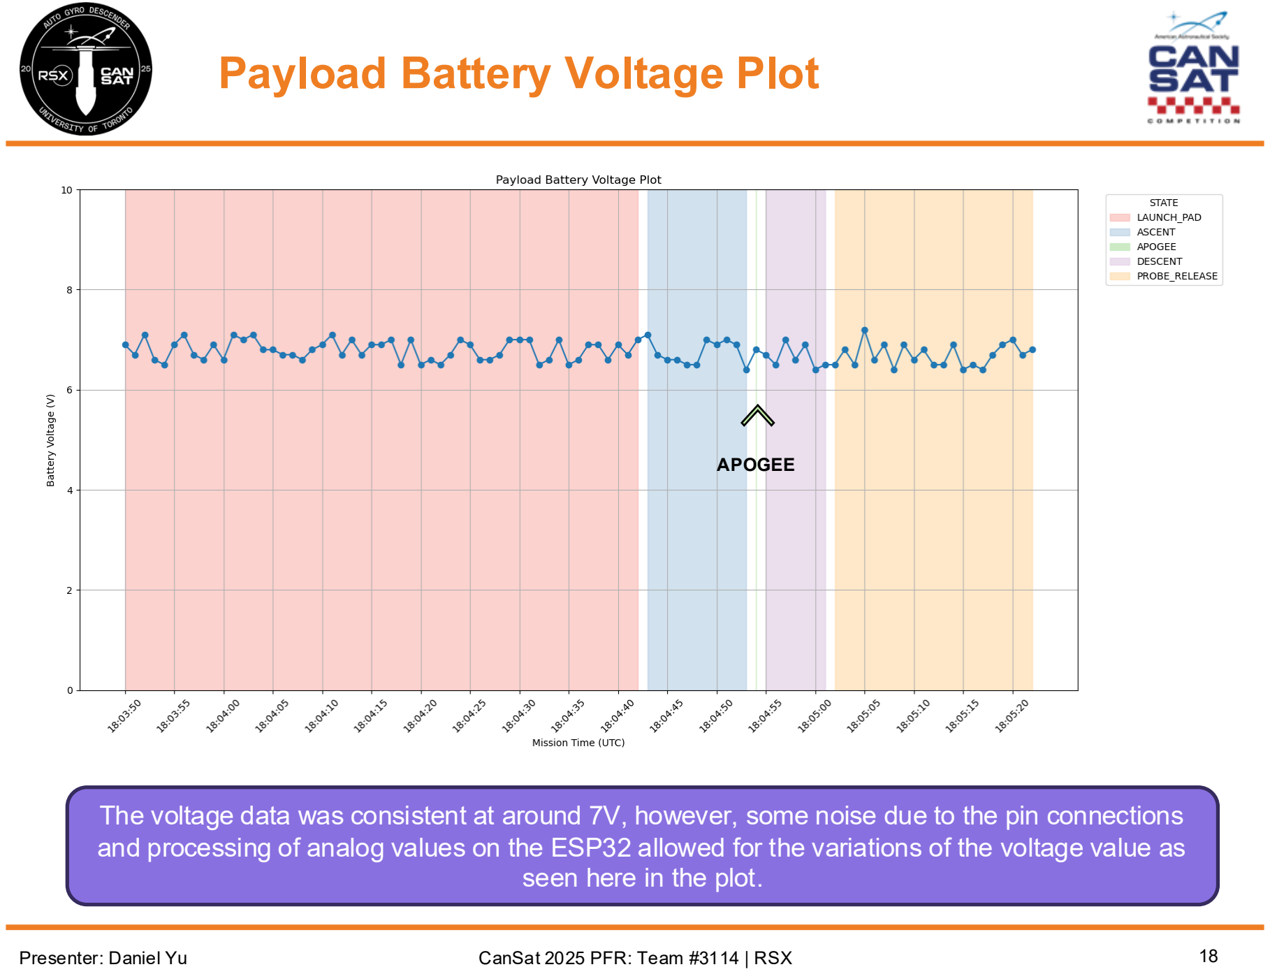
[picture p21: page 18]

Presenter: Daniel Yu

The voltage data was consistent at around 7V, however, some noise due to the pin connections and processing of analog values on the ESP32 allowed for the variations of the voltage value as seen here in the plot.

APOGEE

## Payload Tilt Sensor Plots/Ground Camera Stability (1/3)

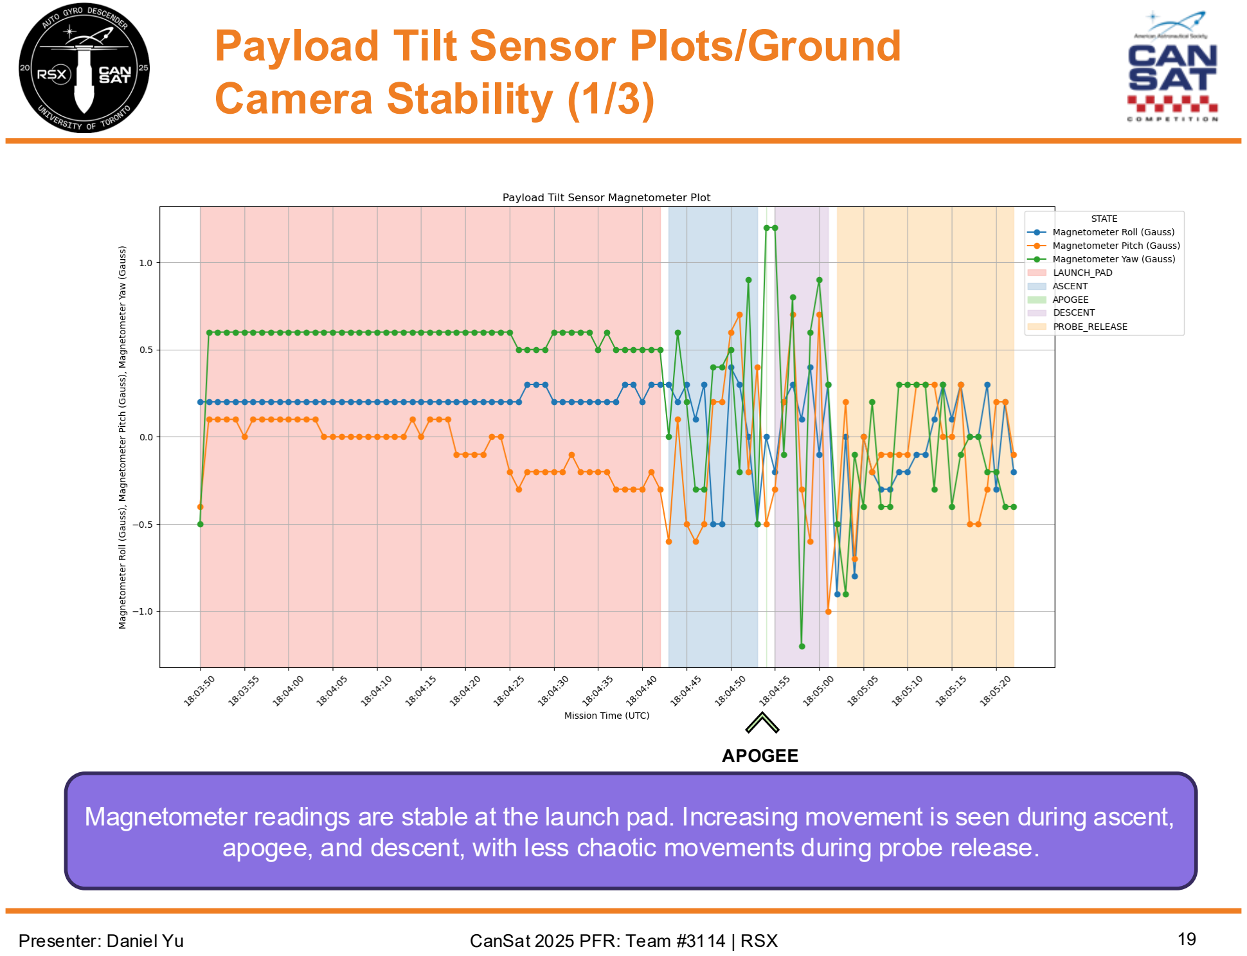
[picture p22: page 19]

Presenter: Daniel Yu

Magnetometer readings are stable at the launch pad. Increasing movement is seen during ascent, apogee, and descent, with less chaotic movements during probe release.

APOGEE

## Payload Tilt Sensor Plots/Ground Camera Stability (2/3)

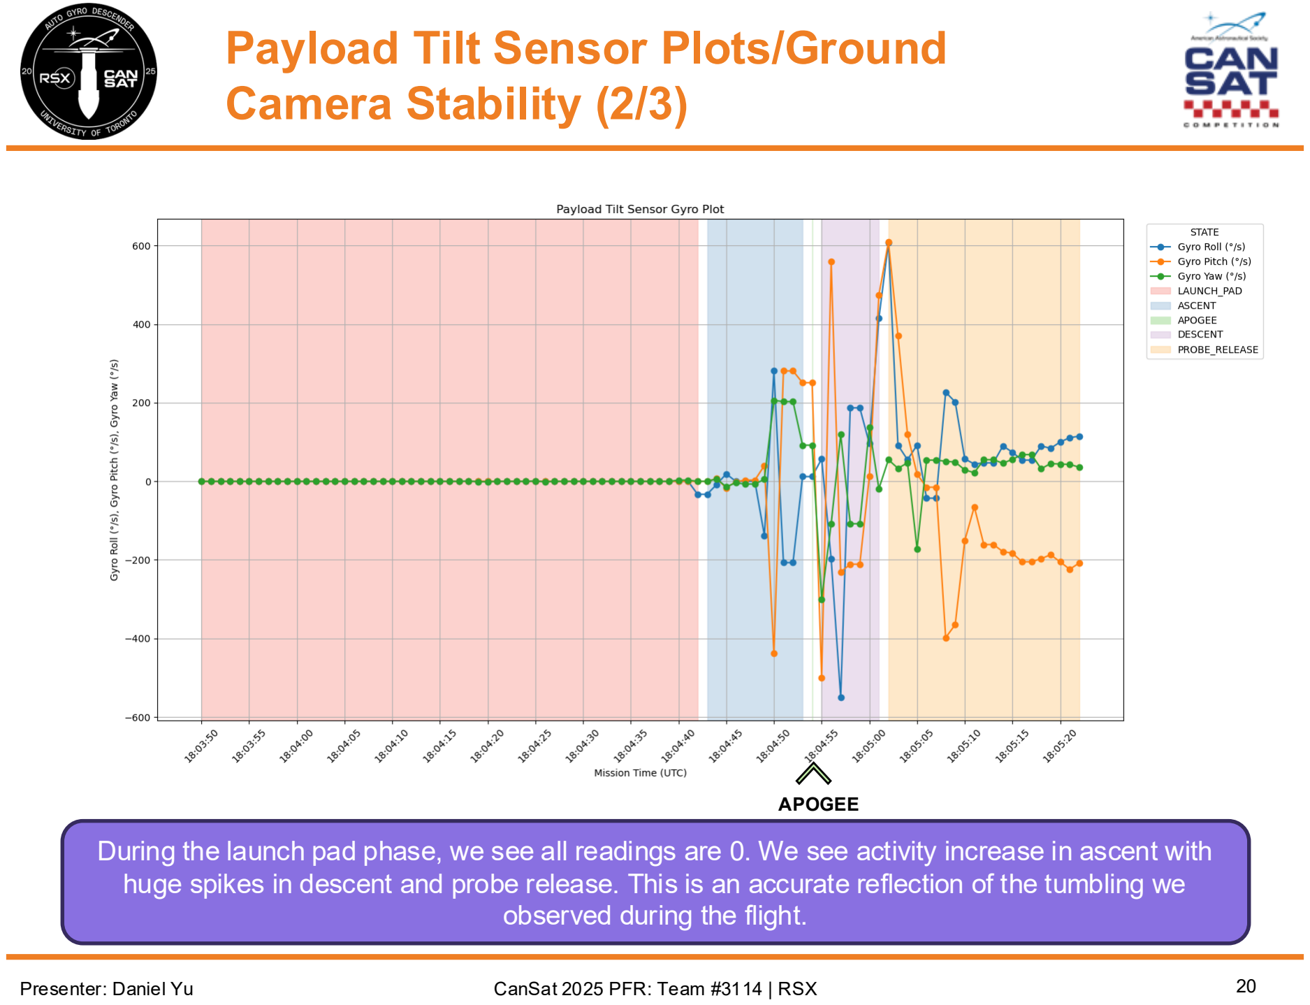
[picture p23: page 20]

Presenter: Daniel Yu

During the launch pad phase, we see all readings are 0. We see activity increase in ascent with huge spikes in descent and probe release. This is an accurate reflection of the tumbling we observed during the flight.

APOGEE

## Payload Tilt Sensor Plots/Ground Camera Stability (3/3)

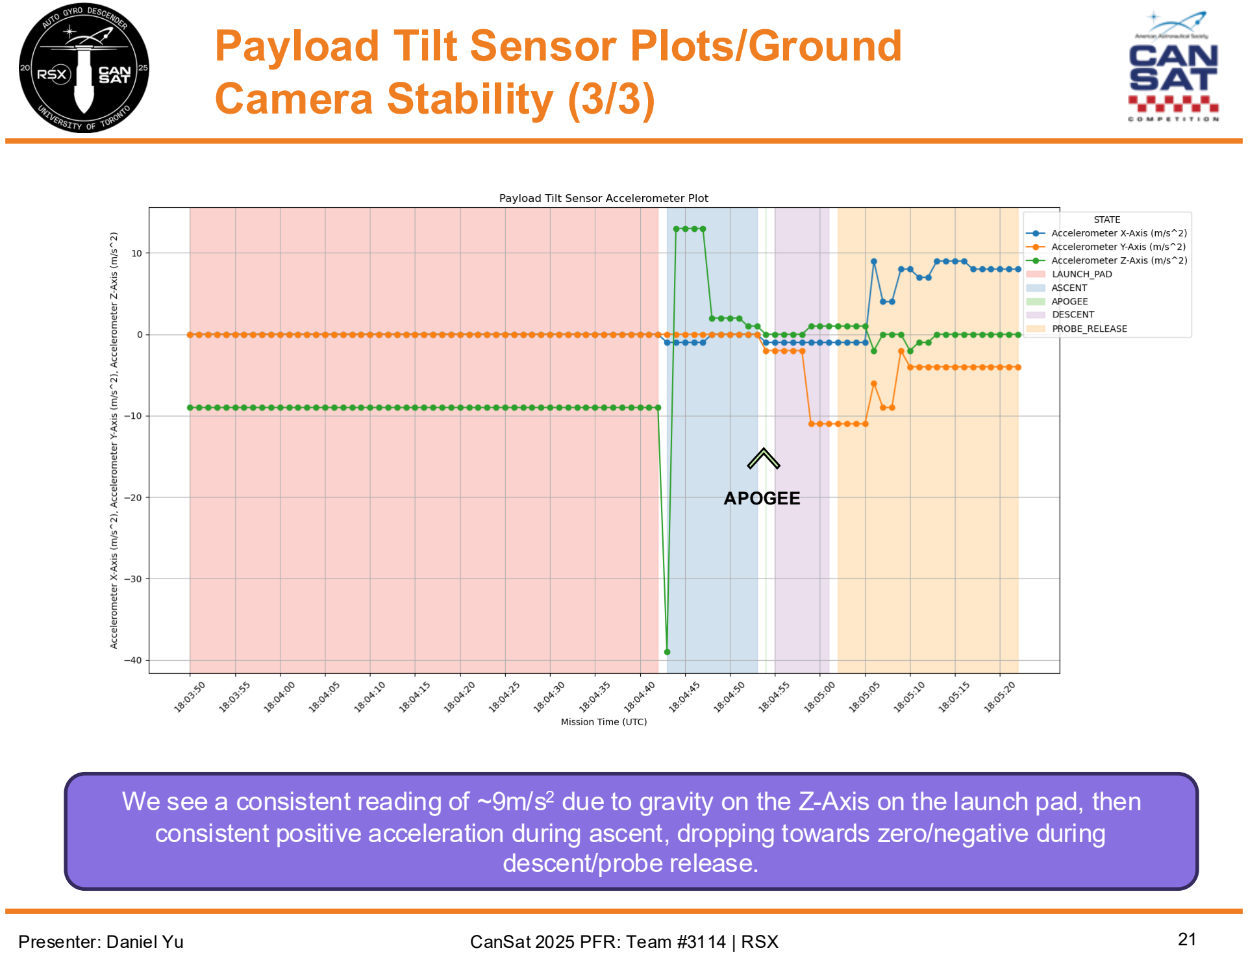
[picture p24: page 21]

Presenter: Daniel Yu

We see a consistent reading of ~9m/s² due to gravity on the Z-Axis on the launch pad, then consistent positive acceleration during ascent, dropping towards zero/negative during descent/probe release.

APOGEE

## Payload GPS Position Plot

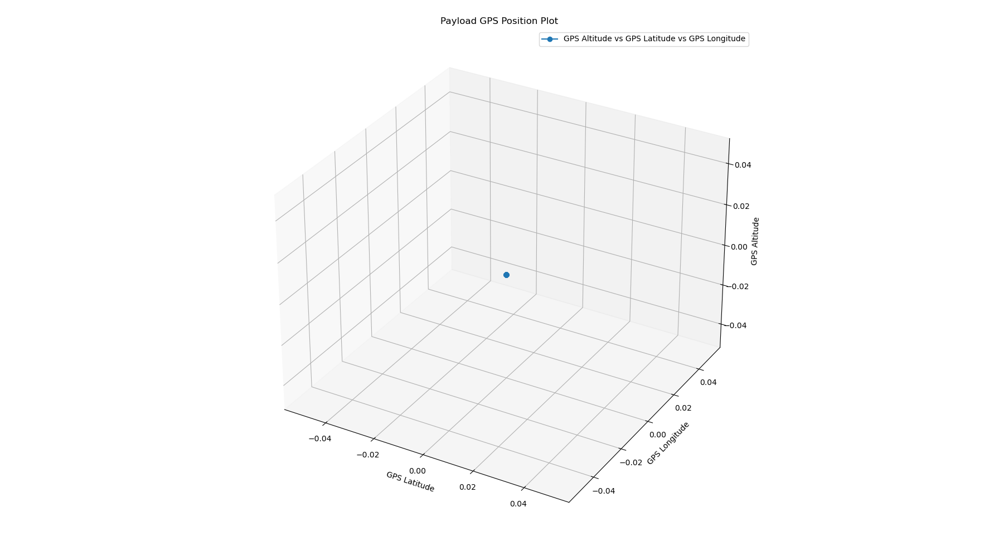
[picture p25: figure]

Presenter: Daniel Yu

Due to a last-minute failure of our BN-220 GPS module, we had to integrate a NEO-6M GPS module donated to us by the University of Hawai’i CanSat team. Unfortunately, this GPS did not receive a single fix on any satellites throughout the entirety of the launch even though it did during testing

## Auto-Gyro Rotation Rate Plot

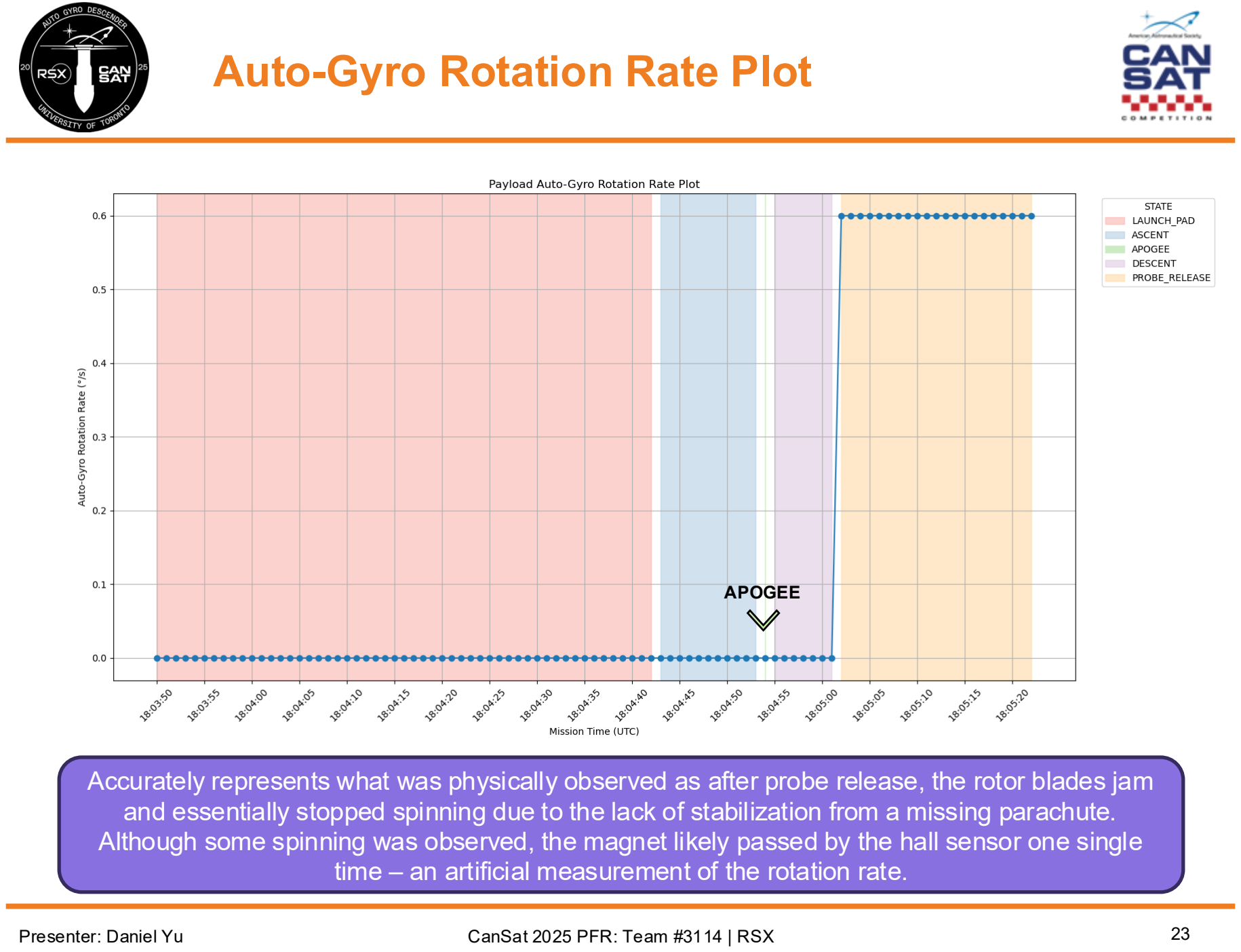
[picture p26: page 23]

Presenter: Daniel Yu

Accurately represents what was physically observed as after probe release, the rotor blades jam and essentially stopped spinning due to the lack of stabilization from a missing parachute. Although some spinning was observed, the magnet likely passed by the hall sensor one single time – an artificial measurement of the rotation rate.

APOGEE

## Payload Release Camera Video


Presenter: Alexey Albert

The camera likely seconds before crashing for the final time (only a small splotch of red/data): https://drive.google.com/file/d/1SEHR9c_Iuld-7ti87NWoYEFy61v4EapE/view?usp=sharing (https://drive.google.com/file/d/1SEHR9c_Iuld-7ti87NWoYEFy61v4EapE/view?usp=sharing)


Struggling camera sensor during CanSat integration (black lines on screen, bright flashes): https://drive.google.com/file/d/1yr0GdckrrTrf2QQrKLBeiR2vzp16YpVA/view?usp=sharing Struggling camera sensor during CanSat
integration (black lines on screen, bright flashes): https://drive.google.com/file/d/1yr0GdckrrTrf2QQrKLBeiR2vzp16YpVA/view?usp=sharing (https://drive.google.com/file/d/1yr0GdckrrTrf2QQrKLBeiR2vzp16YpVA/view?usp=sharing)

Unfortunately, our camera sensors failed to record videos. Our assessment is that due to the extreme air temperature of ~40ºC in the CanSat Payload, the already thermally stressed sensors overheated, resulting in the destruction of the Payload Release Camera, as well as the Ground Camera to crash. This is supported by the steep decline in recording quality during testing as seen in the two recordings attached as well as the significantly worse camera quality in the Ground Camera footage, further discussed in the next slide.

## Ground Camera Video


Presenter: Alexey Albert


As you can see, the images captured on and after launch day with the camera are extremely dark and are primarily only red or blue—in stark contrast to footage recorded prior to the extreme heat of launch day.

Signs of eminent sensor
failure were present when
conducting a postmortem of launch day:
https://drive.google.com/file/d/10pqGMasy4Bveemrgkuo
YIrZsPExTgofy/view?usp=s
haring (https://drive.google.com/file/d/10pqGMasy4BveemrgkuoYIrZsPExTgofy/view?usp=sharing)

Likely the most recently
recorded frames before the sensor permanently failed: https://drive.google.com/file/d/1lr fCSjjWt9cMLMz9yvkIMIQQvBz5 fMV1/view?usp=sharing (https://drive.google.com/file/d/1lrfCSjjWt9cMLMz9yvkIMIQQvBz5fMV1/view?usp=sharing)

The appearance of footage
recorded with the Ground
Camera prior to launch day for reference:
https:// (https://drive.google.com/file/d/1SapZ7BgK9RTjxkdH8Ko7na3ef_32PFTB/view?usp=sharing)drive.google.com (https://drive.google.com/file/d/1SapZ7BgK9RTjxkdH8Ko7na3ef_32PFTB/view?usp=sharing)/file/ d/1SapZ7BgK9RTjxkdH8Ko
7na3ef_32PFTB/ (https://drive.google.com/file/d/1SapZ7BgK9RTjxkdH8Ko7na3ef_32PFTB/view?usp=sharing)view?usp (https://drive.google.com/file/d/1SapZ7BgK9RTjxkdH8Ko7na3ef_32PFTB/view?usp=sharing)=
sharing (https://drive.google.com/file/d/1SapZ7BgK9RTjxkdH8Ko7na3ef_32PFTB/view?usp=sharing)

# Failure Analysis

## Adam Kabbara

## Identification of Failures, Root Causes, Corrective Actions

1. Failed to retain parachute; 2. Failed to hold all rotors; 3. Failed to point cams north; 4. Cams failed mid mission

Presenter: Adam Kabbara

Ejection charge wrongly timed possibly due to slow motor start- up. This caused an early ejection at high speed; The parachute was exposed to much greater loads than expected, causing the parachute cord to rip through its attachment points and separate the parachute from the container; This caused the container to rapidly tumble causing the payload to tumble as well and not deploy all rotors correctly

During the flight, our
ground station was
ready to send a
command to manually
release the payload in
case of a problem with
the flight software. This
did not end up being
needed.

Launch Video:
https://drive.google.com/file/d/1cjAtmRTXh1Y_zpiC4Dni
ZekwGRUozfjr/view?usp= (https://drive.google.com/file/d/1cjAtmRTXh1Y_zpiC4DniZekwGRUozfjr/view?usp=drivesdk)dr
ivesdk (https://drive.google.com/file/d/1cjAtmRTXh1Y_zpiC4DniZekwGRUozfjr/view?usp=drivesdk)

## Identification of Corrective Actions

Presenter: Adam Kabbara

Upgrade Parachute Strength and Testing Procedures
- Select a more robust parachute capable of withstanding higher-than-expected loads at apogee.
- Conduct stress testing beyond nominal conditions to simulate worst-case deployment scenarios.

Improve Thermal Management and Environmental Testing
- Implement active or more effective passive cooling systems instead of relying solely on airflow during descent and limited runtime.
- Conduct full environmental testing on all systems, including thermal testing of components such as onboard cameras.
- Note: Camera thermal testing was omitted due to incomplete test specifications; this must be addressed in future protocols.

Reduce Payload Mass from internal Shroud Usage
- Consider using a lighter shroud or removing it entirely.
- While the shroud offers aerodynamic benefits and helps protect the electronics, the added mass negatively impacts payload efficiency and system performance.

Secure Sensor Mounting and Improve Mechanical Integration
- Avoid relying on header pins for securing electronics, especially for critical components like the XBee.
- Sensors with mounting holes should continue using standoffs; however, for modules without mounting features, design and implement 3D-printed enclosures or brackets to ensure mechanical stability.
- Bolting down all sensors improves durability, reliability, and resistance to vibration/shock during flight.

# Lessons Learned

## Arthur Goetzke-Coburn, Gianluca Ceccacci, & Adam Kabbara

## Discussion of What Worked and What Didn’t

Presenter: Arthur Goetzke-Coburn & Gianluca Ceccacci

What Worked:

Custom-Built Antenna successfully communicated with the XBee on the payload and was easily hand-held.

Custom PCBs were effective, yielding good space utilization.

Altitude data was accurate, and the logic was correct. This lead to the Auto-Gyro successfully decoupling from the CC at 75% of apogee where the rotor blades successfully lifted as anticipated after a proper quick release.

The fiber glass composite rotor blades were very strong and survived impact.

Altitude, Magnetometer, Hall Effect, and temperature data was accurate.

Buzzer survived impact with the ground – JST connectors are effective.

The internal structure of the payload survived impact with relatively minimal damage, protecting the sensors from damage.

What Didn’t Work:

ESP32s were unreliable microcontrollers, making them difficult to work with and requiring frequent replacement.

Lightweight ASA was difficult to print and weak (poor layer adhesion and brittleness). It should not have been used for small prints that require increased structural integrity such as our gearbox supports.

Fiber glass layup rotor blades are ineffective at the hinges of the rotor system, requiring 3D printed attachments for proper integration.

FDM 3D printed gears should be replaced by either metallic gears or potentially resin printed ones.

The cameras failed mid mission -- this demonstrates need for better thermal management and better overall cameras.

The Auto-Gyro system was slow to assemble and needed to be assembled in a specific order, making modifications and testing to certain parts difficult, showing a strong need for better design for assembly.

## Conclusion

31

This year, University of Toronto's RSX made a proud return to CanSat after 9 years of absence. We achieved 2 of our 4 external objectives and successfully launched a payload with custom 15g fiberglass layuped rotors.

Though we faced challenges, including a parachute failure and mid-mission camera loss, we collected valuable data and learned a lot. We also had an amazing time meeting teams from around the world and sharing learning from each other.

Special thanks to the University of Hawai’i team for lending us a GPS last-minute, and to the CanSat organizers and judges for making this a great experience. See you next year!

Presenter: Adam Kabbara | CanSat 2025 PFR: Team #3114 | RSX

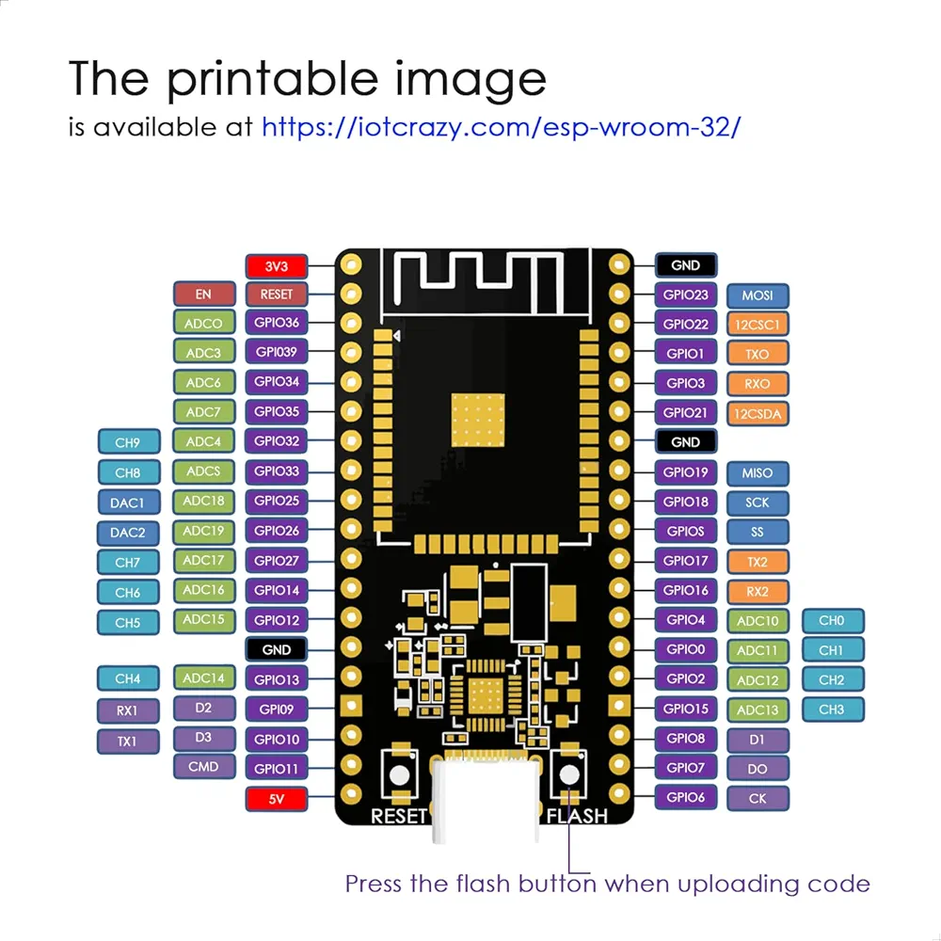
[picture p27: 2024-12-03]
sensor_testing/schematics/drawings/esp32_pinouts.png

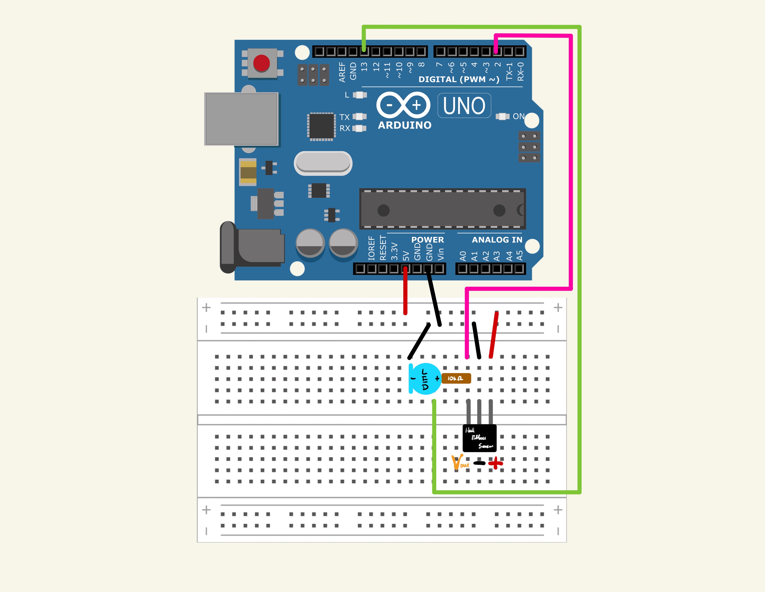
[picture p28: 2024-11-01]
sensor_testing/schematics/drawings/Hall_Effect_Sensor_Schematic.jpg

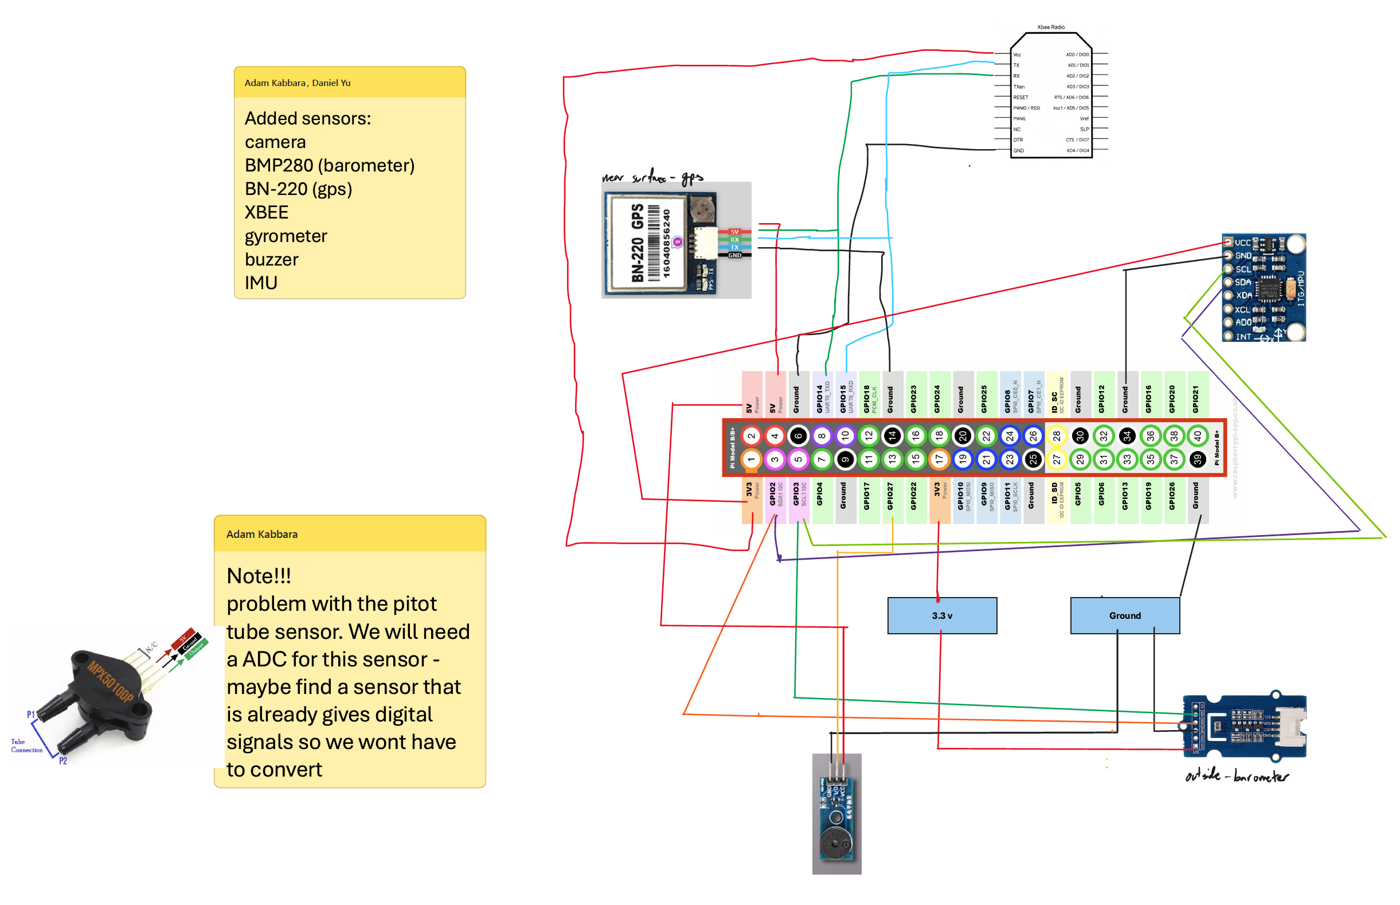
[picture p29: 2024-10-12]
sensor_testing/schematics/drawings/2T3-2T4_Schematic.png

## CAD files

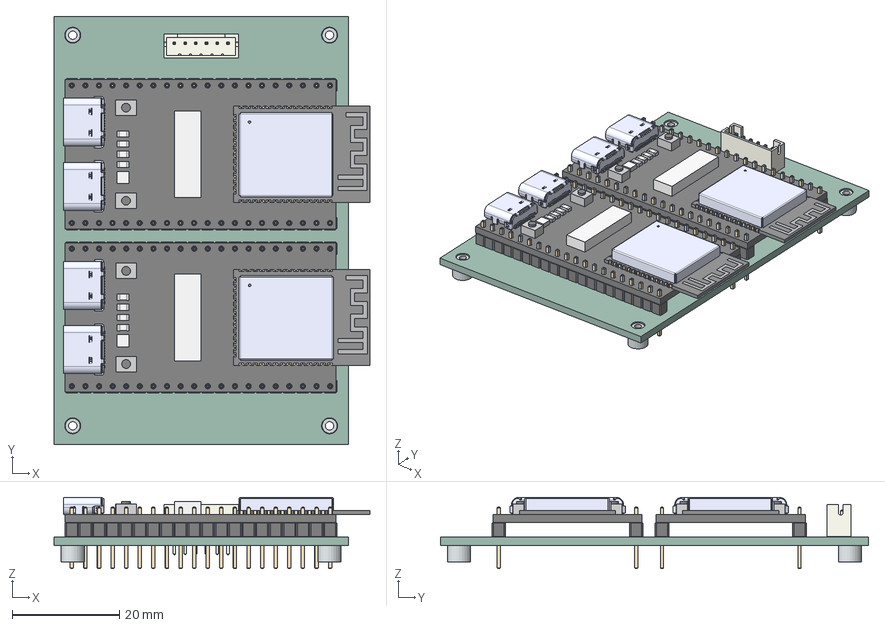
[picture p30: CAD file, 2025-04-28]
circuit_designs/PCBs/Final_Versions/CanSat_Camera_Board/CanSat_Camera_Board.step
59.1 x 80.0 x 13.3 mm
Freenove ESP32 S3 WROOM CAM Board v4 x 2
PinHeader_1x20_P254mm_Vertical x 4
ESP32-S3-WROOM-1-N8R2 x 2
USB-C Female Connector v2 x 4
JST_B6B_PH_K
9774030243R_M2_Standoff v2 x 4
CanSat_Camera_Board_PCB

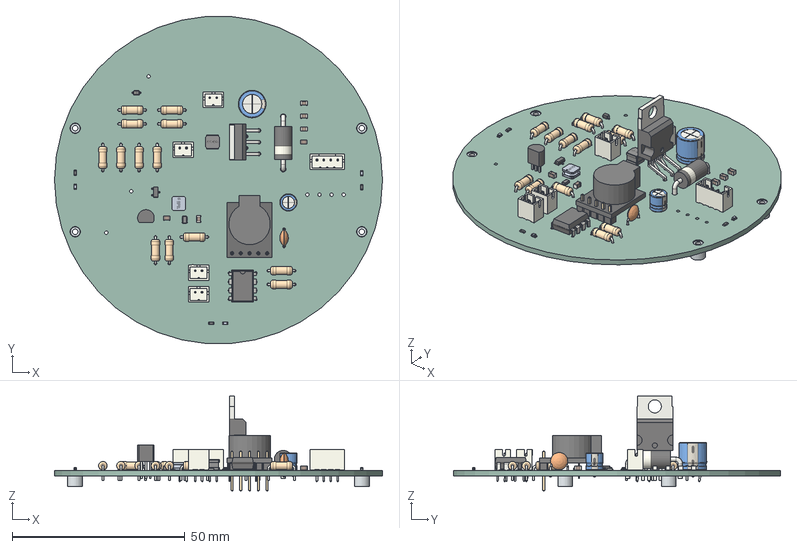
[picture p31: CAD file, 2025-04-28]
circuit_designs/PCBs/Final_Versions/CanSat_Power_Management_Board/CanSat_Power_Management_Board.step
95.0 x 94.7 x 27.5 mm
Assem1 x 4
R_Axial_DIN0207_L63mm_D25mm_P762mm_Horizontal x 13
DIP-8_W7.62mm
CP_Radial_D80mm_P350mm
C_0805_2012Metric x 6
D_DO-201AD_P15.24mm_Horizontal
R_0603_1608Metric x 3
C_Disc_D50mm_W25mm_P500mm
JST_B2B_PH_K x 4
PinHeader_1x05_P254mm_Vertical
Matek Lost Model Beeper v8
CP_Radial_D50mm_P250mm
DRL8
JST_B4B_PH_K
TO-92_Inline_Narrow
TO_220_5_Pentawatt_Multiwatt_5_Vertical_StaggeredType1
SOT_23
ASPI-4030S
D_SOD_323
9774030243R_M2_Standoff v2 x 4
CanSat_Power_Management_Board_PCB

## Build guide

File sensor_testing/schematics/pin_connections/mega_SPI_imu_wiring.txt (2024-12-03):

GND -> GND (shocker)
VCC -> 3.3 V
SCL -> 52 (DIGITAL)
SDA -> 50 (DIGITAL)
ADD -> 51 (DIGITAL)
CS  -> 10 (PUM)
INT -> 9 (PUM)
RST -> 5 (PUM)
PS1 -> 3.3 V

Motor
Orange wire -> 3 (PUM)
Red wire    -> 5 V
Brown wire  -> GND

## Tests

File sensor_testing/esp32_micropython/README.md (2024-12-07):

# Micropython Camera on ESP32 S3 WROOM
## Downloading firmware 
1. downlaod the micro python .bin file from https://micropython.org/download/ESP32_GENERIC_S3/ this link is specific to our esp32 type (Firmware (Support for Octal-SPIRAM)).
2. to get the camera module, you either install the driver for the camera using thoney onto the esp32 or use the firmware provided by the git repo that has the drivers pre installed in the firmware. https://github.com/cnadler86/micropython-camera-API/releases (this is the method we chose in this documentation)

## Downloading `esptool`
1. Just `pip install esptool`. Gonna use this tool to flash firmware onto the esp32

## Flashing
1. Ensure that your ESP32 is in flash mode while you're trying to upload the firmware. To enter flash mode, hold down the `BOOT` button while resetting the board or powering it on.
2. After you have pluged in, on windows, to check what port the esp32 is using go to `Device Manager` and look under the `Ports` drop down menue. In the commands below, `COM6` was the port used.
3. Look for where `esptools` was installed and `cd` there. For my case I installed it in a conda env and it was found in `C:\Users\adamk\anaconda3\envs\cansat\Scripts>`. The commads below use `esptool.exe` but for you it might be `esptool.py`
4. Remove the old fiirmware by running
```
esptool.exe --port COM6 erase_flash
```
5. Install the new firmware by running
```
esptool.exe --chip esp32s3 --baud 115200 --port COM6 write_flash -z 0 "dir_to_firmmware_.bin_file"
```
Now this should take a min or two and you should have the miropython firmware on the esp32.

## Installing dependancies
```
pip install mpremote
```
then use (COM6 is the port connected to esp32)
```
mpremote connect COM6 mip install package-name
```
get packages from here https://github.com/micropython/micropython-lib/tree/master

## Programming
1. Download Thonny https://thonny.org/
2. Set it up by going into `Tools > Options > Interpreter` Then select `Micropython (ESP32)` and select what port it is using in my case `COM6`
3. Test if everything is working by running the [led_blinkning](testing_camera.py)
4. check out the datasheet and change the vars in the testing_camera.py file

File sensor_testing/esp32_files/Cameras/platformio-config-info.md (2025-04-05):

# platformio project info

- using the official `platformio/platform-espressif32` platform doesn't provide the necessary libraries so we have to use `pioarduino/platform-espressif32`
- the board config is a custom board/json for the ESP32S3 Dev Board with 16MB flash and 8MB psram.
- UPDATE: core v3.1.0 seems to have broken the frame buffer when trying to get images, resulting in it being streched vertically with horizontal black lines.
    - Reverted to release #187e1cbaed5888158d65c5dc24100c6d3cc65cb2 (v3.0.4) since thats the last version I checked that it worked on. Newer versons before v3.1.0 might also work.

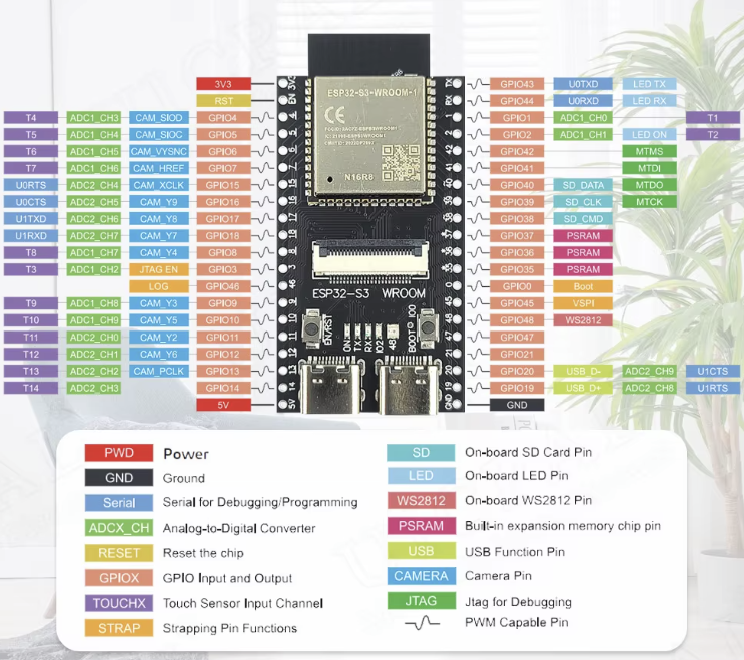
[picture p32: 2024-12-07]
sensor_testing/esp32_micropython/datasheet.png

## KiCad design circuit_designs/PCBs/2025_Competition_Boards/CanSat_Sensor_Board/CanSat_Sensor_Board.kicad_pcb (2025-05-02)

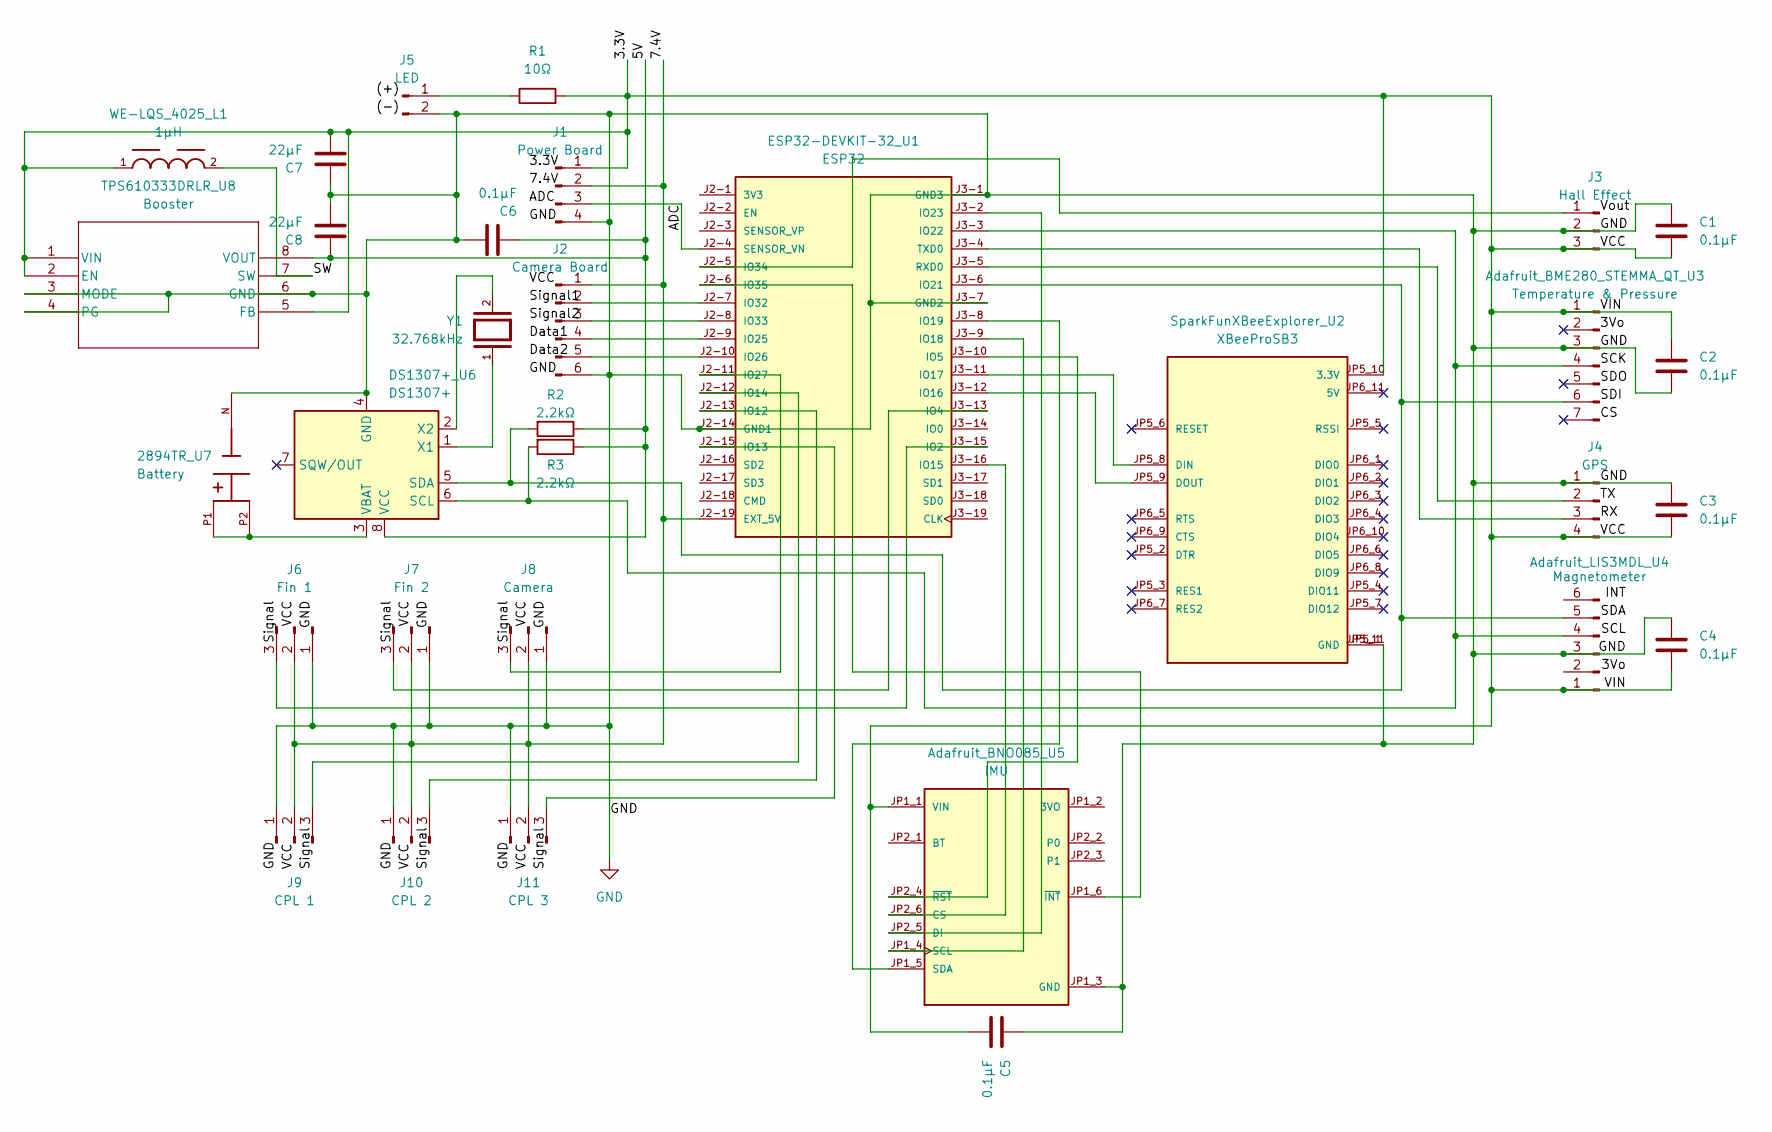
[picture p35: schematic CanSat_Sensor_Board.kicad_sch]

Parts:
2894TR_U7: Battery; BAT_2894TR; PARTREV B
Adafruit_BME280_STEMMA_QT_U3: Temperature & Pressure; Adafruit_BME280_STEMMA_QT
Adafruit_BNO085_U5: IMU; Adafruit_BNO085; PARTREV 2021-03-16
Adafruit_LIS3MDL_U4: Magnetometer; Adafruit_LIS3MDL
C1, C2, C3, C4, C5, C6: 0.1μF; C_0805_2012Metric_Pad1.18x1.45mm_HandSolder
C7, C8: 22μF; C_0805_2012Metric_Pad1.18x1.45mm_HandSolder
DS1307+_U6: DS1307+; DIP-8_W7.62mm
ESP32-DEVKIT-32_U1: ESP32; ESP32-WROOM-32D_Dev_Board; PARTREV V4
J1: Power Board; JST_PH_B4B-PH-K_1x04_P2.00mm_Vertical
J2: Camera Board; JST_PH_B6B-PH-K_1x06_P2.00mm_Vertical
J3: Hall Effect; JST_PH_B3B-PH-K_1x03_P2.00mm_Vertical
J4: GPS; JST_PH_B4B-PH-K_1x04_P2.00mm_Vertical
J5: LED; JST_PH_B2B-PH-K_1x02_P2.00mm_Vertical
J6: Fin 1; JST_PH_B3B-PH-K_1x03_P2.00mm_Vertical
J7: Fin 2; JST_PH_B3B-PH-K_1x03_P2.00mm_Vertical
J8: Camera; JST_PH_B3B-PH-K_1x03_P2.00mm_Vertical
J9: CPL 1; JST_PH_B3B-PH-K_1x03_P2.00mm_Vertical
J10: CPL 2; JST_PH_B3B-PH-K_1x03_P2.00mm_Vertical
J11: CPL 3; JST_PH_B3B-PH-K_1x03_P2.00mm_Vertical
R1: 10Ω; R_0603_1608Metric_Pad0.98x0.95mm_HandSolder
R2, R3: 2.2kΩ; R_Axial_DIN0207_L6.3mm_D2.5mm_P7.62mm_Horizontal
SparkFunXBeeExplorer_U2: XBeeProSB3; SparkFun_XBee_Explorer_Regulated; PARTREV v21
TPS610333DRLR_U8: Booster; SOT-5X3-8_DRL_TEX
WE-LQS_4025_L1: 1μH; WE-LQS_4025
Y1: 32.768kHz; XTAL_AB38T-32.768KHZ

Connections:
/3.3V: Adafruit_BME280_STEMMA_QT_U3.1, Adafruit_BNO085_U5.JP1_1 (VIN), Adafruit_LIS3MDL_U4.1, C1.2, C2.1, C3.2, C4.2, C5.2, C7.2, J1.1, J3.3, J4.4, R1.2, SparkFunXBeeExplorer_U2.JP5_10 (3.3V), TPS610333DRLR_U8.1 (VIN), TPS610333DRLR_U8.2 (EN), TPS610333DRLR_U8.5 (FB), WE-LQS_4025_L1.1
/5V: C6.2, C8.1, DS1307+_U6.8 (VCC), R2.1, R3.1, TPS610333DRLR_U8.8 (VOUT)
/7.4V: ESP32-DEVKIT-32_U1.J2-19 (EXT_5V), J1.2, J2.1, J6.2, J7.2, J8.2, J9.2, J10.2, J11.2
/ADC: ESP32-DEVKIT-32_U1.J2-4 (SENSOR_VN), J1.3
/SW: TPS610333DRLR_U8.7 (SW), WE-LQS_4025_L1.2
GND: 2894TR_U7.N, Adafruit_BME280_STEMMA_QT_U3.3, Adafruit_BNO085_U5.JP1_3 (GND), Adafruit_LIS3MDL_U4.3, C1.1, C2.2, C3.1, C4.1, C5.1, C6.1, C7.1, C8.2, DS1307+_U6.4 (GND), ESP32-DEVKIT-32_U1.J2-14 (GND1), ESP32-DEVKIT-32_U1.J3-1 (GND3), ESP32-DEVKIT-32_U1.J3-7 (GND2), J1.4, J2.6, J3.2, J4.1, J5.2, J6.1, J7.1, J8.1, J9.1, J10.1, J11.1, SparkFunXBeeExplorer_U2.JP5_1 (GND), SparkFunXBeeExplorer_U2.JP5_11 (GND), TPS610333DRLR_U8.3 (MODE), TPS610333DRLR_U8.4 (PG), TPS610333DRLR_U8.6 (GND)
unnamed: Adafruit_BME280_STEMMA_QT_U3.4, Adafruit_LIS3MDL_U4.4, DS1307+_U6.6 (SCL), ESP32-DEVKIT-32_U1.J3-3 (IO22), R3.2
unnamed: Adafruit_BME280_STEMMA_QT_U3.6, Adafruit_LIS3MDL_U4.5, DS1307+_U6.5 (SDA), ESP32-DEVKIT-32_U1.J3-6 (IO21), R2.2
unnamed: Adafruit_BNO085_U5.JP2_6 (CS), ESP32-DEVKIT-32_U1.J3-16 (IO15)
unnamed: Adafruit_BNO085_U5.JP2_5 (DI), ESP32-DEVKIT-32_U1.J3-2 (IO23)
unnamed: Adafruit_BNO085_U5.JP1_4 (SCL), ESP32-DEVKIT-32_U1.J3-9 (IO18)
unnamed: Adafruit_BNO085_U5.JP1_5 (SDA), ESP32-DEVKIT-32_U1.J3-8 (IO19)
unnamed: Adafruit_BNO085_U5.JP1_6 (~INT), ESP32-DEVKIT-32_U1.J2-6 (IO35)
unnamed: Adafruit_BNO085_U5.JP2_4 (~RST), ESP32-DEVKIT-32_U1.J3-10 (IO5)
unnamed: 2894TR_U7.P1, 2894TR_U7.P2, DS1307+_U6.3 (VBAT)
unnamed: DS1307+_U6.1 (X1), Y1.1
unnamed: DS1307+_U6.2 (X2), Y1.2
unnamed: ESP32-DEVKIT-32_U1.J3-15 (IO2), J6.3
unnamed: ESP32-DEVKIT-32_U1.J3-13 (IO4), J7.3
unnamed: ESP32-DEVKIT-32_U1.J2-13 (IO12), J10.3
unnamed: ESP32-DEVKIT-32_U1.J2-15 (IO13), J11.3
unnamed: ESP32-DEVKIT-32_U1.J2-12 (IO14), J9.3
unnamed: ESP32-DEVKIT-32_U1.J3-12 (IO16), SparkFunXBeeExplorer_U2.JP5_9 (DOUT)
unnamed: ESP32-DEVKIT-32_U1.J3-11 (IO17), SparkFunXBeeExplorer_U2.JP5_8 (DIN)
unnamed: ESP32-DEVKIT-32_U1.J2-9 (IO25), J2.4
unnamed: ESP32-DEVKIT-32_U1.J2-10 (IO26), J2.5
unnamed: ESP32-DEVKIT-32_U1.J2-11 (IO27), J8.3
unnamed: ESP32-DEVKIT-32_U1.J2-7 (IO32), J2.2
unnamed: ESP32-DEVKIT-32_U1.J2-8 (IO33), J2.3
unnamed: ESP32-DEVKIT-32_U1.J2-5 (IO34), J3.1
unnamed: ESP32-DEVKIT-32_U1.J3-5 (RXD0), J4.2
unnamed: ESP32-DEVKIT-32_U1.J3-4 (TXD0), J4.3
unnamed: J5.1, R1.1

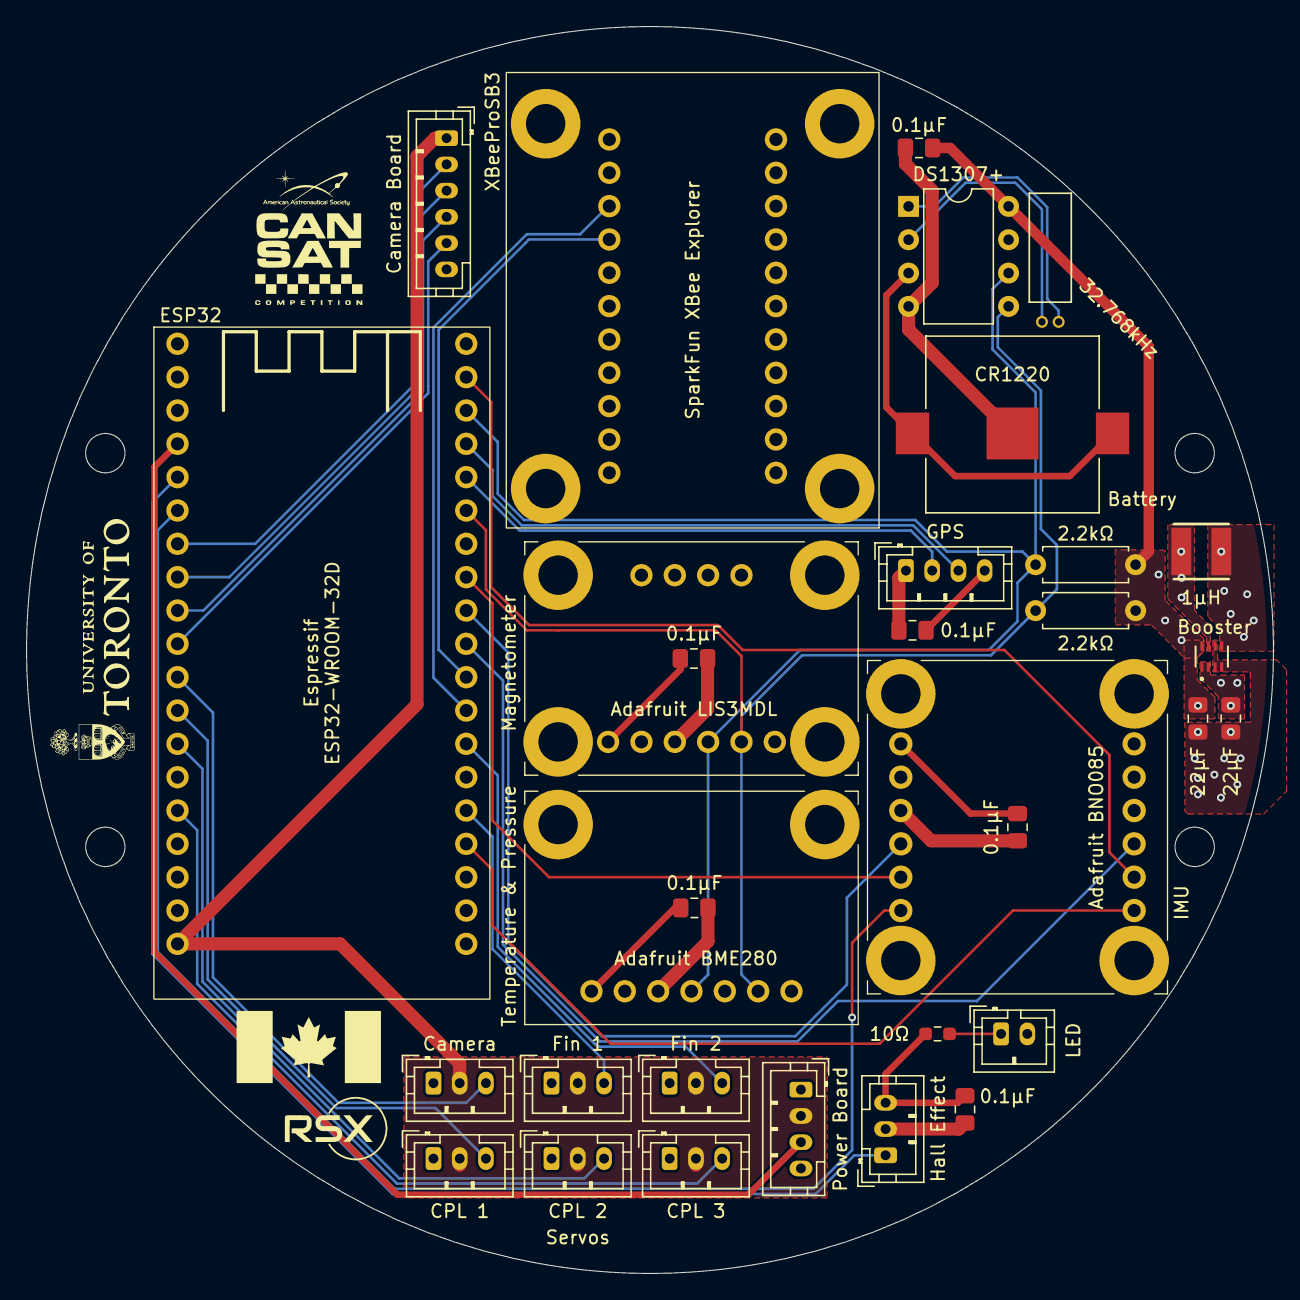
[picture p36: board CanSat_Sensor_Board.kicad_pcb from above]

Board: 4 copper layers, 95.0 x 95.0 mm, 32 parts (0 on the bottom side), 33 nets.

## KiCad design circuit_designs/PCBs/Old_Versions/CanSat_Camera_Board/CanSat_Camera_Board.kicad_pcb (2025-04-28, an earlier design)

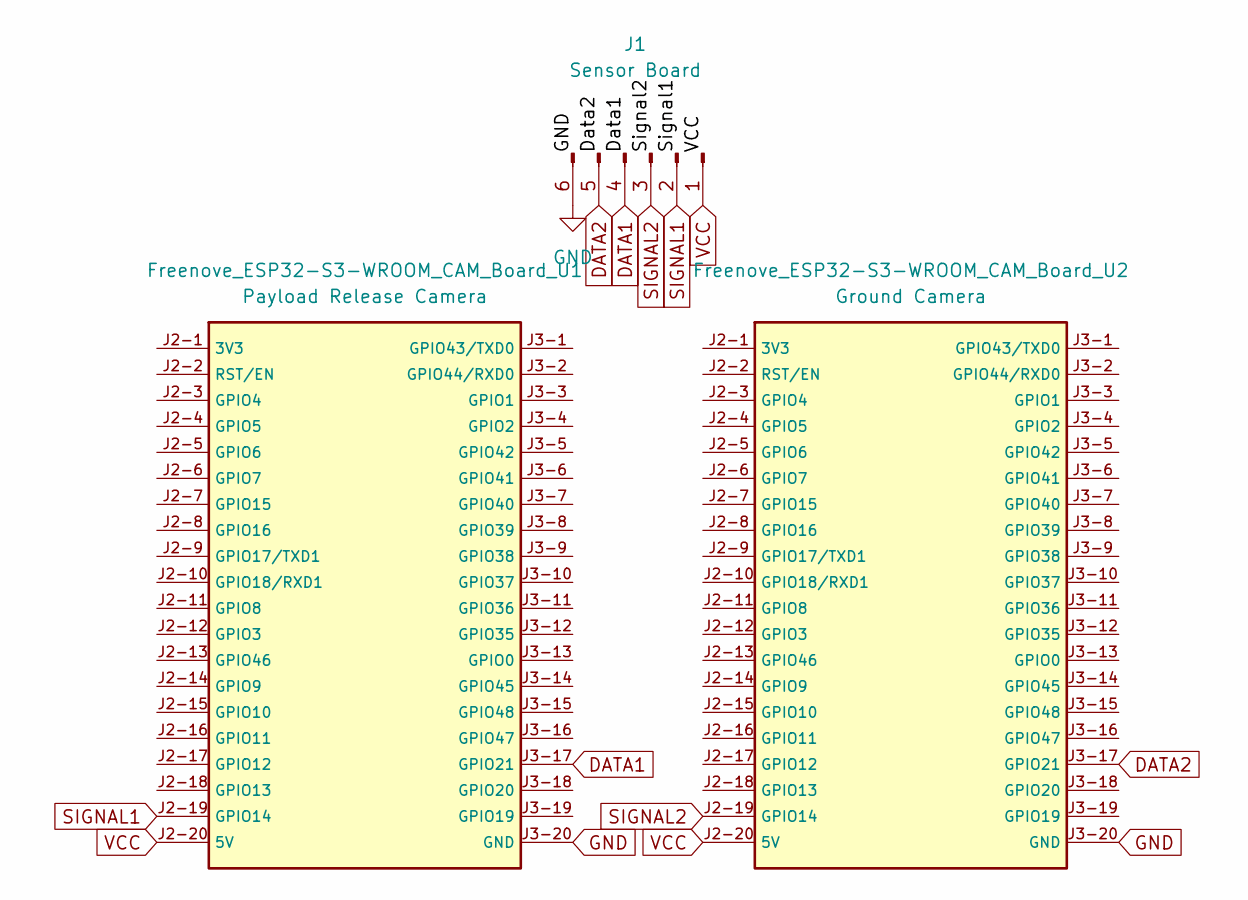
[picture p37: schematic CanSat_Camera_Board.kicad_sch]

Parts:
Freenove_ESP32-S3-WROOM_CAM_Board_U1: Payload Release Camera; Freenove_ESP32-S3-WROOM_CAM_Board
Freenove_ESP32-S3-WROOM_CAM_Board_U2: Ground Camera; Freenove_ESP32-S3-WROOM_CAM_Board
J1: Sensor Board; JST_PH_B6B-PH-K_1x06_P2.00mm_Vertical

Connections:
DATA1: Freenove_ESP32-S3-WROOM_CAM_Board_U1.J3-17 (GPIO21), J1.4
DATA2: Freenove_ESP32-S3-WROOM_CAM_Board_U2.J3-17 (GPIO21), J1.5
GND: Freenove_ESP32-S3-WROOM_CAM_Board_U1.J3-20 (GND), Freenove_ESP32-S3-WROOM_CAM_Board_U2.J3-20 (GND), J1.6
SIGNAL1: Freenove_ESP32-S3-WROOM_CAM_Board_U1.J2-19 (GPIO14), J1.2
SIGNAL2: Freenove_ESP32-S3-WROOM_CAM_Board_U2.J2-19 (GPIO14), J1.3
VCC: Freenove_ESP32-S3-WROOM_CAM_Board_U1.J2-20 (5V), Freenove_ESP32-S3-WROOM_CAM_Board_U2.J2-20 (5V), J1.1

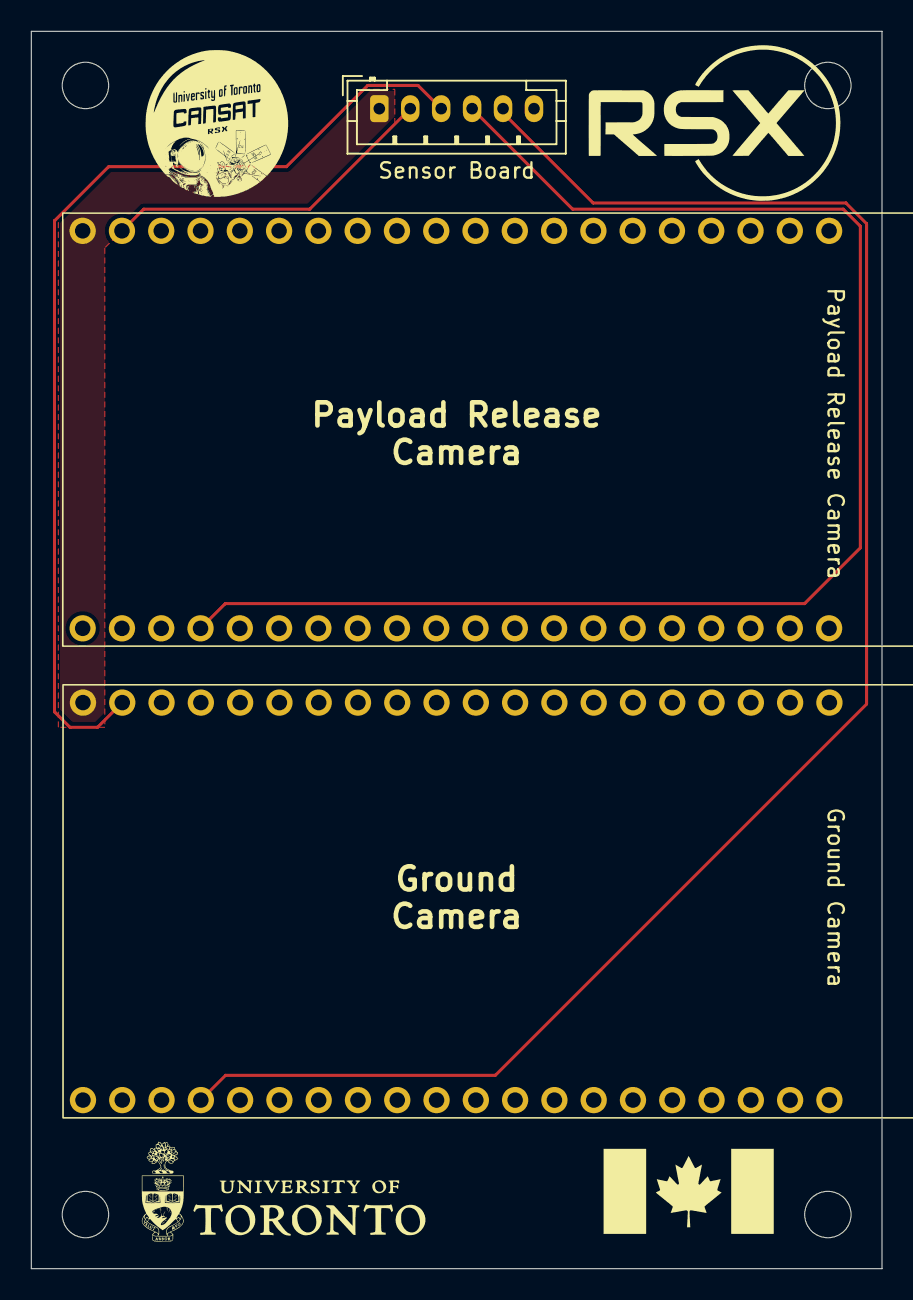
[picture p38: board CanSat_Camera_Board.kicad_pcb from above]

Board: 2 copper layers, 55.0 x 80.0 mm, 3 parts (0 on the bottom side), 6 nets.

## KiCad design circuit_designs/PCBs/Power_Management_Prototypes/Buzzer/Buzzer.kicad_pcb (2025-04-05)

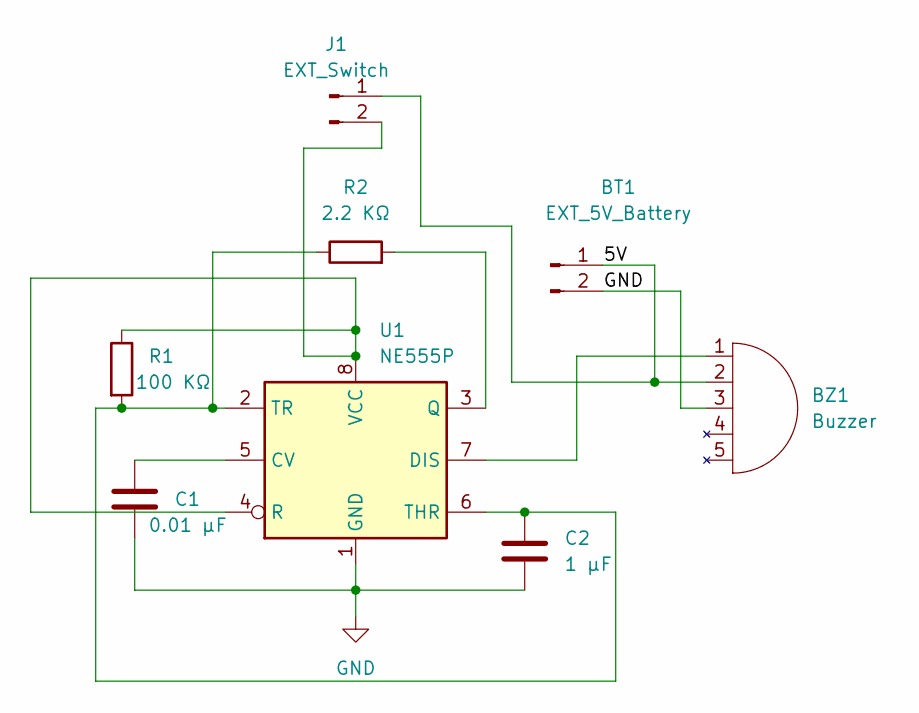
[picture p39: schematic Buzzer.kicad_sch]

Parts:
BT1: EXT_5V_Battery; External_Connection_2pin
BZ1: Buzzer; Buzzer_Connection
C1: 0.01 μF; CP_Axial_L11.0mm_D5.0mm_P18.00mm_Horizontal
C2: 1 μF; CP_Axial_L10.0mm_D6.0mm_P15.00mm_Horizontal
J1: EXT_Switch; External_Connection_2pin
R1: 100 KΩ; R_Axial_DIN0207_L6.3mm_D2.5mm_P10.16mm_Horizontal
R2: 2.2 KΩ; R_Axial_DIN0207_L6.3mm_D2.5mm_P10.16mm_Horizontal
U1: NE555P; DIP-8_W7.62mm

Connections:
/5V: BT1.1, BZ1.2 (5V), J1.1
GND: BT1.2, BZ1.3 (G), C1.2, C2.2, U1.1 (GND)
unnamed: BZ1.1 (Aux), U1.7 (DIS)
unnamed: J1.2, R1.1, U1.4 (R), U1.8 (VCC)
unnamed: C1.1, U1.5 (CV)
unnamed: R2.2, U1.3 (Q)
unnamed: C2.1, R1.2, R2.1, U1.2 (TR), U1.6 (THR)

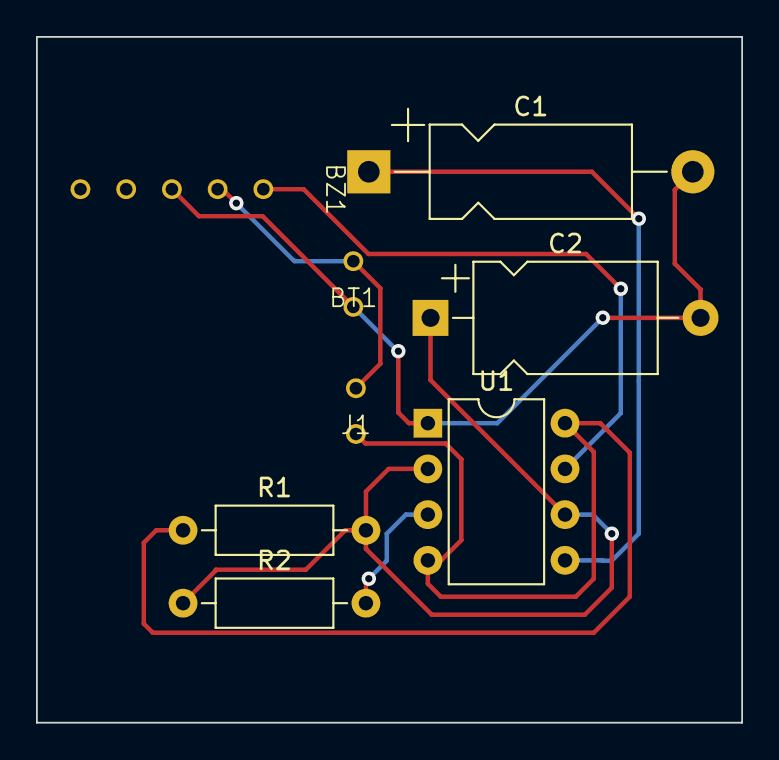
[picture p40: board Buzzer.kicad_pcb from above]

Board: 2 copper layers, 39.2 x 38.1 mm, 8 parts (0 on the bottom side), 7 nets.

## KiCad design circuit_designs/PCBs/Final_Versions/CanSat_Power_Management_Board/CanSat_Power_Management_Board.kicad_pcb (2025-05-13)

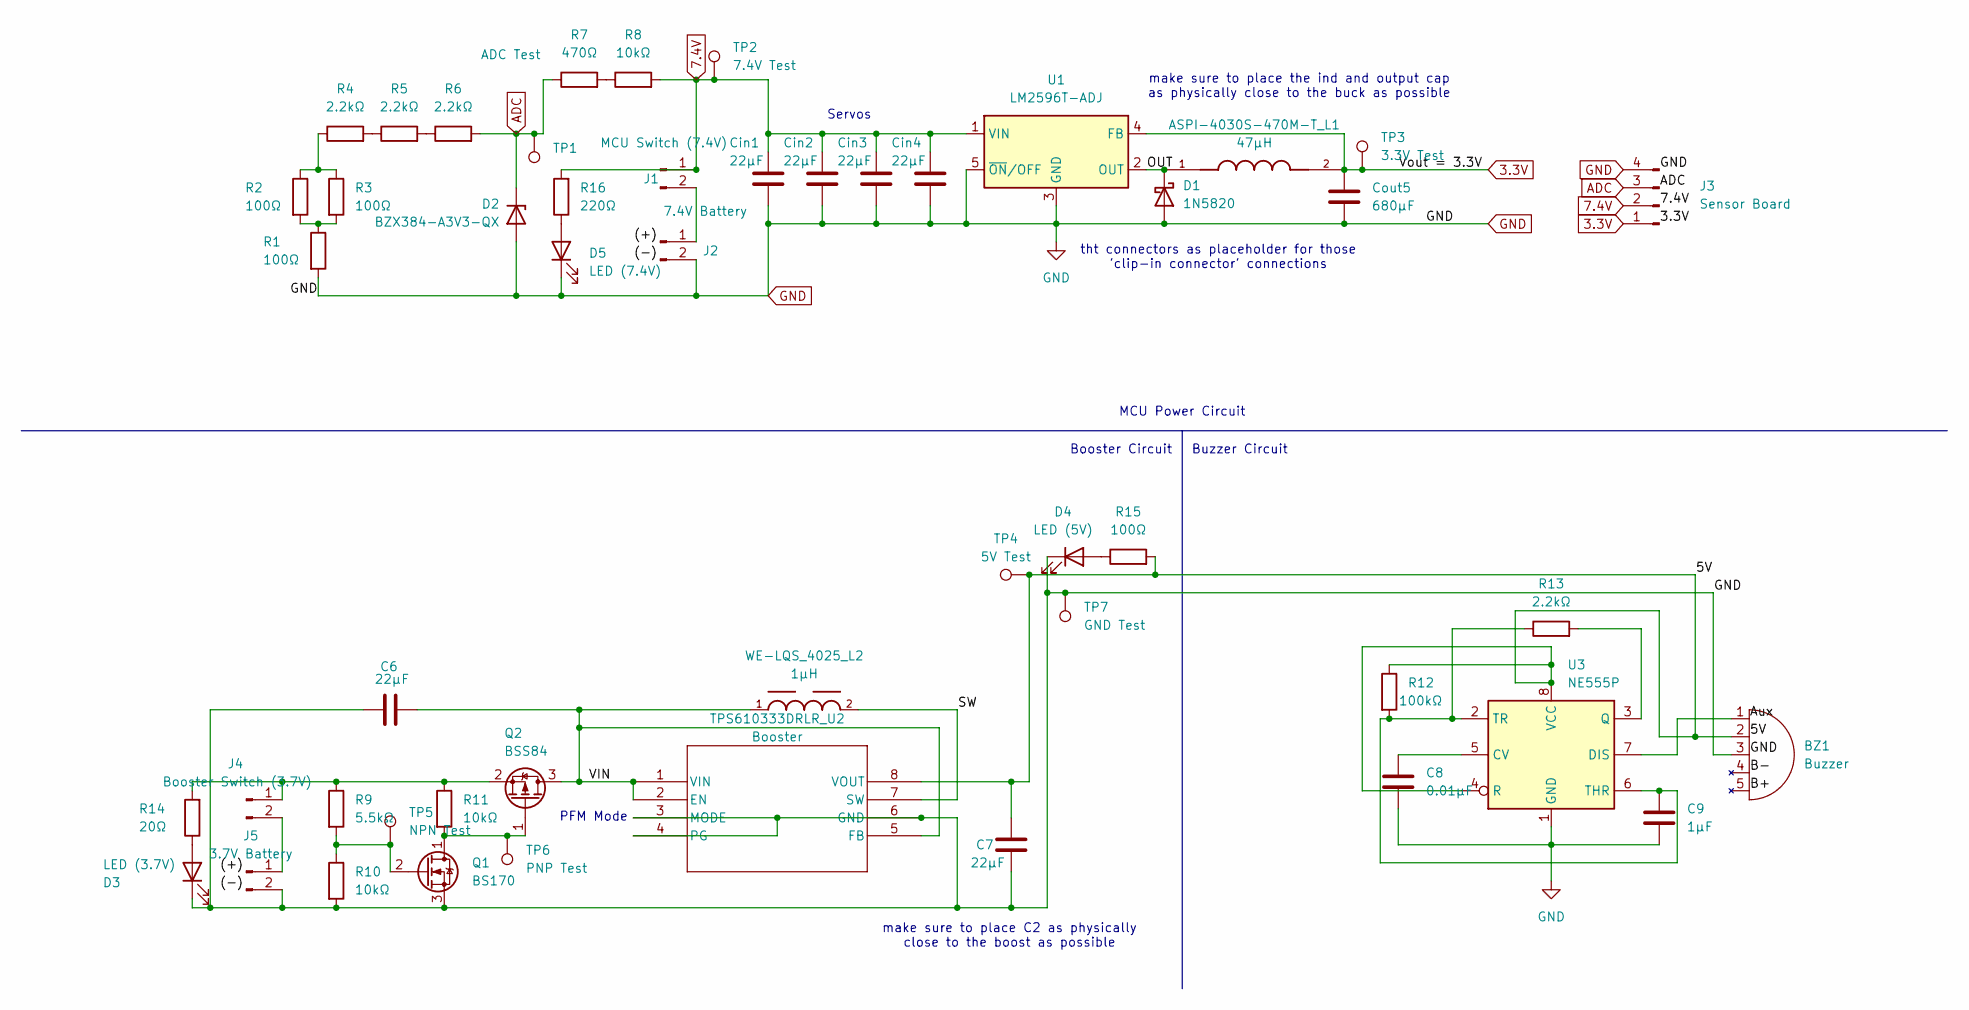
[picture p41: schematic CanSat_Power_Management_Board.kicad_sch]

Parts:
ASPI-4030S-470M-T_L1: 47μH; IND_ASPI-4030S-470M-T; PARTREV 03.09.13
BZ1: Buzzer; Matek_Lost_Model_Beeper
C6, C7: 22μF; C_0805_2012Metric_Pad1.18x1.45mm_HandSolder
C8: 0.01μF; C_Disc_D5.0mm_W2.5mm_P5.00mm
C9: 1μF; CP_Radial_D5.0mm_P2.50mm
Cin1, Cin2, Cin3, Cin4: 22μF; C_0805_2012Metric_Pad1.18x1.45mm_HandSolder
Cout5: 680μF; CP_Radial_D8.0mm_P3.50mm
D1: 1N5820; D_DO-201AD_P15.24mm_Horizontal
D2: BZX384-A3V3-QX; D_SOD-323_HandSoldering
D3: LED (3.7V); WL-SMCW_0603
D4: LED (5V); WL-SMCW_0603
D5: LED (7.4V); WL-SMCW_0603
J1: MCU Switch (7.4V); JST_PH_B2B-PH-K_1x02_P2.00mm_Vertical
J2: 7.4V Battery; JST_PH_B2B-PH-K_1x02_P2.00mm_Vertical
J3: Sensor Board; JST_PH_B4B-PH-K_1x04_P2.00mm_Vertical
J4: Booster Switch (3.7V); JST_PH_B2B-PH-K_1x02_P2.00mm_Vertical
J5: 3.7V Battery; JST_PH_B2B-PH-K_1x02_P2.00mm_Vertical
Q1: BS170; TO-92_Inline
Q2: BSS84; SOT-23
R1, R2, R3: 100Ω; R_Axial_DIN0207_L6.3mm_D2.5mm_P7.62mm_Horizontal
R4, R5, R6, R13: 2.2kΩ; R_Axial_DIN0207_L6.3mm_D2.5mm_P7.62mm_Horizontal
R7: 470Ω; R_Axial_DIN0207_L6.3mm_D2.5mm_P7.62mm_Horizontal
R8, R10, R11: 10kΩ; R_Axial_DIN0207_L6.3mm_D2.5mm_P7.62mm_Horizontal
R9: 5.5kΩ; R_Axial_DIN0207_L6.3mm_D2.5mm_P7.62mm_Horizontal
R12: 100kΩ; R_Axial_DIN0207_L6.3mm_D2.5mm_P7.62mm_Horizontal
R14: 20Ω; R_0603_1608Metric_Pad0.98x0.95mm_HandSolder
R15: 100Ω; R_0603_1608Metric_Pad0.98x0.95mm_HandSolder
R16: 220Ω; R_0603_1608Metric_Pad0.98x0.95mm_HandSolder
TP1: ADC Test; TestPoint_THTPad_2.0x2.0mm_Drill1.0mm
TP2: 7.4V Test; TestPoint_THTPad_2.0x2.0mm_Drill1.0mm
TP3: 3.3V Test; TestPoint_THTPad_2.0x2.0mm_Drill1.0mm
TP4: 5V Test; TestPoint_THTPad_2.0x2.0mm_Drill1.0mm
TP5: NPN Test; TestPoint_THTPad_2.0x2.0mm_Drill1.0mm
TP6: PNP Test; TestPoint_THTPad_2.0x2.0mm_Drill1.0mm
TP7: GND Test; TestPoint_THTPad_2.0x2.0mm_Drill1.0mm
TPS610333DRLR_U2: Booster; SOT-5X3-8_DRL_TEX
U1: LM2596T-ADJ; TO-220-5_P3.4x3.7mm_StaggerOdd_Lead3.8mm_Vertical
U3: NE555P; DIP-8_W7.62mm
WE-LQS_4025_L2: 1μH; WE-LQS_4025

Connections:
3.3V: ASPI-4030S-470M-T_L1.2, Cout5.1, J3.1, TP3.1, U1.4 (FB)
7.4V: Cin1.1, Cin2.1, Cin3.1, Cin4.1, J1.1, J3.2, R8.2, R16.2, TP2.1, U1.1 (VIN)
/5V: BZ1.2 (5V), C7.1, R12.1, R15.2, TP4.1, TPS610333DRLR_U2.8 (VOUT), U3.4 (R), U3.8 (VCC)
/OUT: ASPI-4030S-470M-T_L1.1, D1.1 (K), U1.2 (OUT)
/SW: TPS610333DRLR_U2.7 (SW), WE-LQS_4025_L2.2
/VIN: C6.1, Q2.3 (D), TPS610333DRLR_U2.1 (VIN), TPS610333DRLR_U2.2 (EN), TPS610333DRLR_U2.5 (FB), WE-LQS_4025_L2.1
ADC: D2.1 (K), J3.3, R6.2, R7.1, TP1.1
GND: BZ1.3 (G), C6.2, C7.2, C8.2, C9.2, Cin1.2, Cin2.2, Cin3.2, Cin4.2, Cout5.2, D1.2 (A), D2.2 (A), D3.1 (K), D4.1 (K), D5.1 (K), J2.2, J3.4, J5.2, Q1.3 (S), R1.2, R10.2, TP7.1, TPS610333DRLR_U2.3 (MODE), TPS610333DRLR_U2.4 (PG), TPS610333DRLR_U2.6 (GND), U1.3 (GND), U1.5 (~ON/OFF), U3.1 (GND)
unnamed: BZ1.1 (Aux), U3.7 (DIS)
unnamed: D3.2 (A), R14.1
unnamed: D4.2 (A), R15.1
unnamed: D5.2 (A), R16.1
unnamed: J1.2, J2.1
unnamed: J4.1, Q2.2 (S), R9.1, R11.1, R14.2
unnamed: J4.2, J5.1
unnamed: Q1.1 (D), Q2.1 (G), R11.2, TP6.1
unnamed: Q1.2 (G), R9.2, R10.1, TP5.1
unnamed: R1.1, R2.2, R3.2
unnamed: R2.1, R3.1, R4.1
unnamed: R4.2, R5.1
unnamed: R5.2, R6.1
unnamed: R7.2, R8.1
unnamed: C8.1, U3.5 (CV)
unnamed: R13.2, U3.3 (Q)
unnamed: C9.1, R12.2, R13.1, U3.2 (TR), U3.6 (THR)

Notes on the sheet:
Buzzer Circuit
tht connectors as placeholder for those 'clip-in connector' connections
Booster Circuit
Servos
PFM Mode
make sure to place C2 as physically close to the boost as possible
make sure to place the ind and output cap as physically close to the buck as possible
MCU Power Circuit

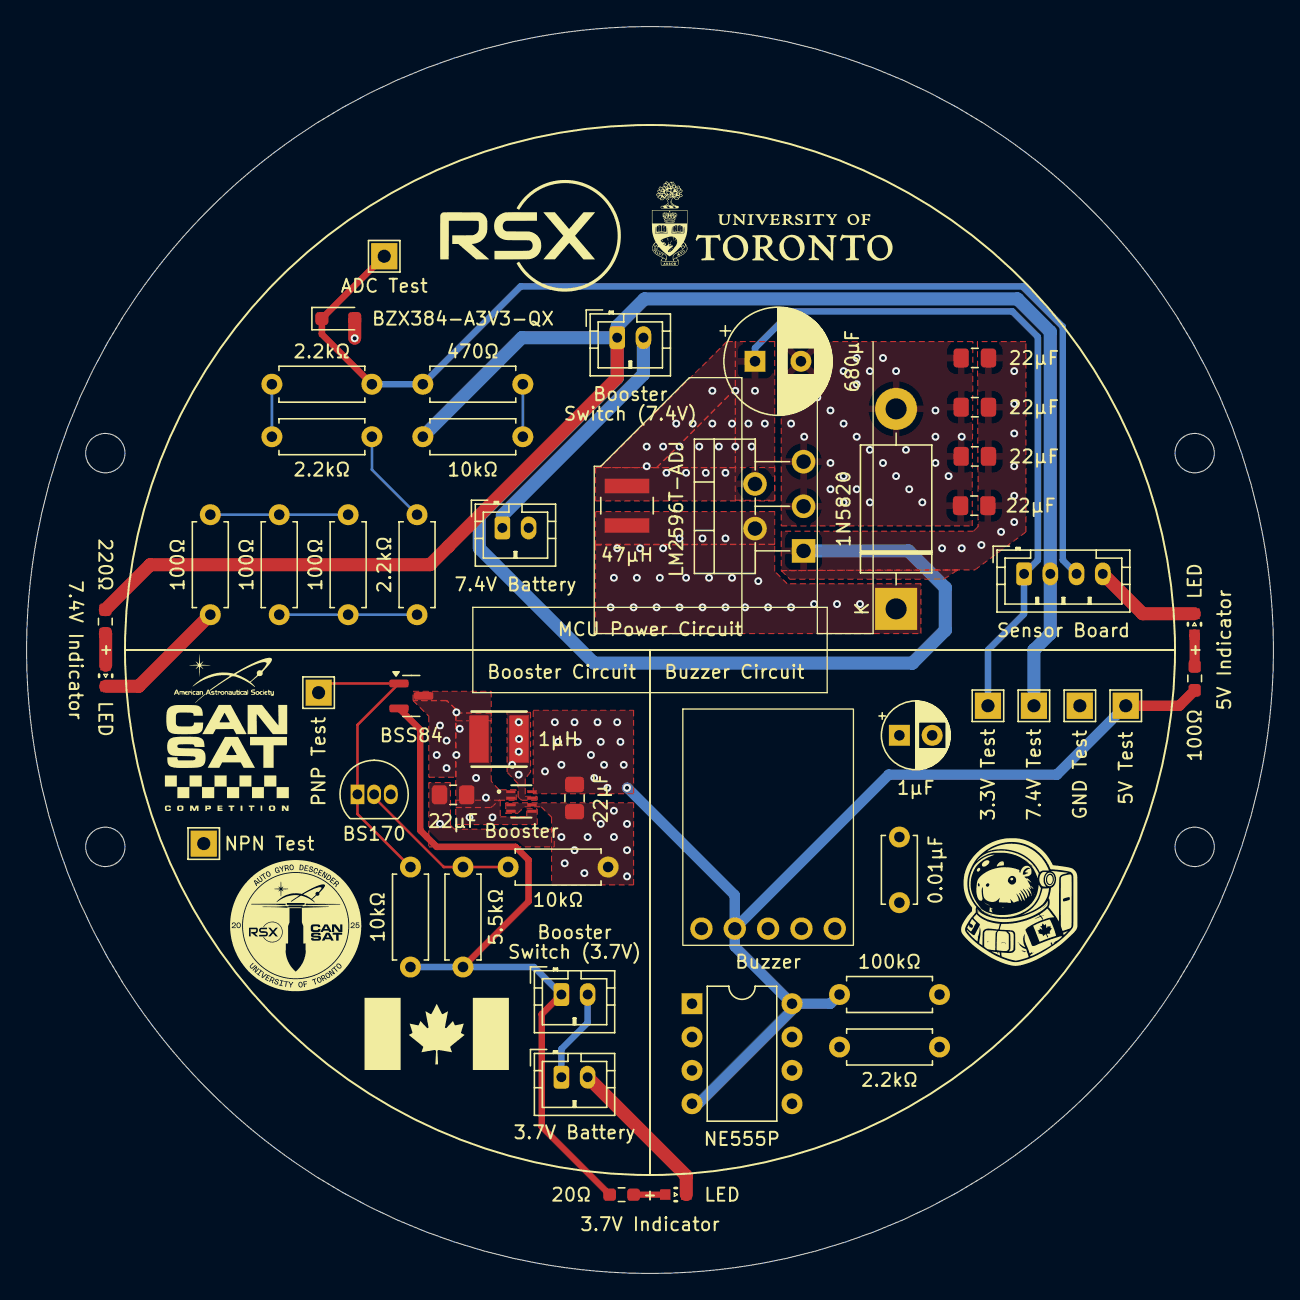
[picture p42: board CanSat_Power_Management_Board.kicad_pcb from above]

Board: 4 copper layers, 95.0 x 95.0 mm, 50 parts (0 on the bottom side), 25 nets.

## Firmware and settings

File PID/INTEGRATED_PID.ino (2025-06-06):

#include <Arduino.h>
#include <ESP32Servo.h>  // ESP32‐compatible Servo library
#include <Adafruit_BNO08x.h>
#include <Adafruit_LIS3MDL.h>
#include <Wire.h>
#include <SPI.h>
#include <math.h>

// ─── Servo Pin Definitions ───────────────────────────────────────────────────
static const int SERVO_LEFT_PIN  = 2;  // GPIO pin for left fin (adjust as needed)
static const int SERVO_RIGHT_PIN = 4;  // GPIO pin for right fin (adjust as needed)

// ─── Servo Objects ────────────────────────────────────────────────────────────
Servo servoLeft;
Servo servoRight;

// --------------------------
// Simple PID + Stability Monitor
//       for ESP32 (Arduino)
// --------------------------

// ===== PID Controller Class =====
class PID {
public:
  PID(float Kp_, float Ki_, float Kd_, float output_limit_)
    : Kp(Kp_), Ki(Ki_), Kd(Kd_), output_limit(output_limit_),
      integral(0.0f), prev_error(0.0f), prev_time(0)
  {}

  // Call in loop(); returns a fin‐deflection command in degrees (±output_limit)
  float compute(float setpoint_deg, float current_deg) {
    unsigned long now = millis();
    float dt = (prev_time == 0) ? 0.0f : float(now - prev_time) / 1000.0f;
    prev_time = now;

    // Compute angular error in [–180, +180]
    float raw_error = setpoint_deg - current_deg;
    float error = fmod(raw_error + 180.0f, 360.0f) - 180.0f;

    // Provisional derivative (unfiltered)
    float derivative = 0.0f;
    if (dt > 0.0f) {
      float raw_derivative = (error - prev_error) / dt;
      // Simple low‐pass filter on D term
      derivative = der_filter_coeff * raw_derivative
                 + (1.0f - der_filter_coeff) * prev_derivative;
      prev_derivative = derivative;
    }

    // Provisional integral
    float proposed_integral = integral;
    if (dt > 0.0f) {
      proposed_integral += error * dt;
    }

    // Unsaturated output
    float unsat = Kp * error + Ki * proposed_integral + Kd * derivative;

    // Saturate
    float sat = unsat;
    if (sat > output_limit) sat = output_limit;
    if (sat < -output_limit) sat = -output_limit;

    // Anti‐windup: only commit integral if NOT saturated
    if (fabs(unsat) <= output_limit) {
      integral = proposed_integral;
    }

    prev_error = error;
    return sat;
  }

  // Allow external code to adjust gains
  void setGains(float Kp_, float Ki_, float Kd_) {
    Kp = Kp_;
    Ki = Ki_;
    Kd = Kd_;
  }
  void getGains(float &outKp, float &outKi, float &outKd) {
    outKp = Kp; outKi = Ki; outKd = Kd;
  }

private:
  float Kp, Ki, Kd;
  float output_limit;
  float integral;
  float prev_error;
  float prev_derivative = 0.0f;
  const float der_filter_coeff = 0.3f;  // α for D‐term filter
  unsigned long prev_time;              // last millis() timestamp
};


// ===== Simple Auto‐Tuner / Stability Monitor =====
class SimpleAutoTuner {
public:
  // window_size = how many consecutive error samples to check
  // error_threshold = if abs(error) > this after window, trigger
  // adjust_factor = multiply Kp/Kd by this factor when instability detected
  SimpleAutoTuner(PID &pid_ref,
                  uint8_t window_size_ = 5,
                  float error_threshold_ = 2.0f,
                  float adjust_factor_ = 0.8f)
    : pid(pid_ref),
      window_size(window_size_),
      error_threshold(error_threshold_),
      adjust_factor(adjust_factor_),
      head(0),
      count(0)
  {
    // initialize error buffer to zeros
    for (uint8_t i = 0; i < MAX_WINDOW; i++) {
      errors[i] = 0.0f;
    }
  }

  // Call this every control step with absolute error (deg):
  void update(float abs_error) {
    // Push new error into circular buffer
    errors[head] = abs_error;
    head = (head + 1) % window_size;
    if (count < window_size) count++;

    // Only proceed if buffer is full
    if (count < window_size) return;

    // Check if errors are non‐decreasing over the entire window
    bool nonDec = true;
    for (uint8_t i = 1; i < window_size; i++) {
      uint8_t idxPrev = (head + MAX_WINDOW - i - 1) % window_size;
      uint8_t idxCurr = (head + MAX_WINDOW - i) % window_size;
      if (errors[idxCurr] < errors[idxPrev]) {
        nonDec = false;
        break;
      }
    }

    // If error never decreased AND latest error exceeds threshold, reduce gains
    float latestError = errors[(head + MAX_WINDOW - 1) % window_size];
    if (nonDec && latestError > error_threshold) {
      float Kp, Ki, Kd;
      pid.getGains(Kp, Ki, Kd);
      float newKp = Kp * adjust_factor;
      float newKi = Ki;  // leave integral alone
      float newKd = Kd * adjust_factor;
      pid.setGains(newKp, newKi, newKd);
      Serial.printf(
        "[AutoTuner] Instability → Kp: %.3f→%.3f, Ki: %.3f→%.3f, Kd: %.3f→%.3f\n",
        Kp, newKp, Ki, newKi, Kd, newKd
      );
      // Clear buffer so we don’t immediately trigger again
      clearBuffer();
    }
  }

private:
  PID &pid;
  static const uint8_t MAX_WINDOW = 10;  // absolute max size
  uint8_t window_size;
  float error_threshold;
  float adjust_factor;

  float errors[MAX_WINDOW];
  uint8_t head;
  uint8_t count;

  void clearBuffer() {
    for (uint8_t i = 0; i < window_size; i++) {
      errors[i] = 0.0f;
    }
    head = 0;
    count = 0;
  }
};



// ================= GET HEADING (haha head) ======================
// --- BNO08x SPI Pins ---
#define BNO08X_CS 15
#define BNO08X_INT 35
#define BNO08X_RESET 5
#define SPI_SCK 18
#define SPI_MISO 19
#define SPI_MOSI 23

SPIClass mySPI(VSPI);
Adafruit_BNO08x bno08x(BNO08X_RESET);
Adafruit_LIS3MDL lis3mdl;

// Kalman filter state
float yaw_estimate = 0.0;
float yaw_cov = 1.0;
const float Q = 0.01;  // process noise
const float R = 1.0;   // measurement noise
unsigned long lastUpdate = 0;

// Convert BNO08x quaternion to yaw (degrees)
float quaternionToYawDegrees(float r, float i, float j, float k) {
  float yaw = atan2(2.0 * (r * k + i * j), 1.0 - 2.0 * (j * j + k * k));
  float yaw_deg = yaw * 180.0 / PI;
  if (yaw_deg < 0) yaw_deg += 360.0;
  return yaw_deg;
}

// Tilt-compensated heading from magnetometer + accelerometer
float computeTiltCompensatedYaw(float mx, float my, float mz,
                                float ax, float ay, float az) {
  float norm = sqrt(ax * ax + ay * ay + az * az);
  if (norm == 0) return 0;
  ax /= norm;
  ay /= norm;
  az /= norm;

  float pitch = asin(-ax);
  float roll = atan2(ay, az);

  float Xh = mx * cos(pitch) + mz * sin(pitch);
  float Yh = mx * sin(roll) * sin(pitch) + my * cos(roll) - mz * sin(roll) * cos(pitch);

  float heading = atan2(Yh, Xh);
  float heading_deg = heading * 180.0 / PI;
  if (heading_deg < 0) heading_deg += 360.0;
  return heading_deg;
}

// Kalman filter update
void kalmanUpdate(float gyro_z, float mag_yaw, float dt) {
  yaw_estimate += gyro_z * dt * 180.0 / PI;  // convert rad/s to deg/s
  yaw_cov += Q;

  if (yaw_estimate < 0) yaw_estimate += 360.0;
  if (yaw_estimate >= 360.0) yaw_estimate -= 360.0;

  float K = yaw_cov / (yaw_cov + R);
  yaw_estimate += K * (mag_yaw - yaw_estimate);
  yaw_cov *= (1 - K);
}
// Example: read current roll angle (deg) from IMU or other sensor:
float readRollSensor() {
    static float gyroZ = 0;
  static float ax = 0, ay = 0, az = 0;
  float bnoYaw = -1;

  // Timing
  unsigned long now = millis();
  float dt = (now - lastUpdate) / 1000.0;
  lastUpdate = now;

  // Read ONE event (non-blocking)
  sh2_SensorValue_t sensorValue;
  if (bno08x.getSensorEvent(&sensorValue)) {
    switch (sensorValue.sensorId) {
      case SH2_ACCELEROMETER:
        ax = sensorValue.un.accelerometer.x;
        ay = sensorValue.un.accelerometer.y;
        az = sensorValue.un.accelerometer.z;
        break;

      case SH2_GYROSCOPE_CALIBRATED:
        gyroZ = sensorValue.un.gyroscope.z;
        break;

      case SH2_ARVR_STABILIZED_RV:
        bnoYaw = quaternionToYawDegrees(
          sensorValue.un.arvrStabilizedRV.real,
          sensorValue.un.arvrStabilizedRV.i,
          sensorValue.un.arvrStabilizedRV.j,
          sensorValue.un.arvrStabilizedRV.k);
        break;
    }
  }

  // Read LIS3MDL magnetometer
  lis3mdl.read();
  float mx = lis3mdl.x;
  float my = lis3mdl.y;
  float mz = lis3mdl.z;

  float magYaw = computeTiltCompensatedYaw(mx, my, mz, ax, ay, az);

  float pitch = asin(-ax);
  float roll = atan2(ay, az);

  // Kalman filter
  kalmanUpdate(gyroZ, magYaw, dt);


  // Compute how much to rotate to face due north (0°)
  //float angle_to_north = fmod((360.0 - yaw_estimate), 360.0);

  return yaw_estimate;
}



// ===== Global Objects & Configuration =====
const float FIN_LIMIT = 15.0f;   // max fin deflection (±15°)
PID pidController(0.6267, 0, 0.9488, FIN_LIMIT);


void applyFinOutput(float finDeg) {
  // Constrain the requested deflection to ±FIN_LIMIT
  if (finDeg >  FIN_LIMIT) finDeg =  FIN_LIMIT;
  if (finDeg < -FIN_LIMIT) finDeg = -FIN_LIMIT;

  // Compute each servo’s absolute position (0°..180°)
  float angleLeft  = 90.0f + finDeg;  // center at 90°, plus finDeg
  float angleRight = 90.0f - finDeg;  // center at 90°, minus finDeg

  // Constrain to valid servo range [0°, 180°]
  angleLeft  = constrain(angleLeft,  0.0f, 180.0f);
  angleRight = constrain(angleRight, 0.0f, 180.0f);

  // Send commands to the servos
  servoLeft.write(static_cast<int>(angleLeft));
  servoRight.write(static_cast<int>(angleRight));
}
// AutoTuner parameters:
const uint8_t TUNER_WINDOW = 5;     // check last 5 error samples
const float   TUNER_THRESH = 5.0f;  // degrees
const float   TUNER_FACTOR = 0.8f;  // reduce Kp/Kd to 80%
SimpleAutoTuner tuner(pidController, TUNER_WINDOW, TUNER_THRESH, TUNER_FACTOR);


void setup() {
  Serial.begin(115200);
  delay(1000);
  
  servoLeft.attach(SERVO_LEFT_PIN);
  servoRight.attach(SERVO_RIGHT_PIN);
  Serial.println("Starting BNO085 + LIS3MDL Kalman Yaw Fusion");

  // --- BNO08x SPI Init ---
  mySPI.begin(SPI_SCK, SPI_MISO, SPI_MOSI);
  if (!bno08x.begin_SPI(BNO08X_CS, BNO08X_INT, &mySPI)) {
    Serial.println(":x: BNO085 not detected.");
    while (1) delay(1000);
  }
  Serial.println(":white_check_mark: BNO08x initialized over SPI.");

  bno08x.enableReport(SH2_ARVR_STABILIZED_RV);
  bno08x.enableReport(SH2_ACCELEROMETER);
  bno08x.enableReport(SH2_GYROSCOPE_CALIBRATED);

  // --- LIS3MDL I2C Init ---
  if (!lis3mdl.begin_I2C()) {
    Serial.println(":x: LIS3MDL not detected.");
    while (1) delay(1000);
  }
  Serial.println(":white_check_mark: LIS3MDL initialized over I2C.");

  lis3mdl.setPerformanceMode(LIS3MDL_LOWPOWERMODE);
  lis3mdl.setOperationMode(LIS3MDL_CONTINUOUSMODE);
  lis3mdl.setDataRate(LIS3MDL_DATARATE_155_HZ);
  lis3mdl.setRange(LIS3MDL_RANGE_4_GAUSS);
  lis3mdl.setIntThreshold(500);

  lastUpdate = millis();
}


void loop() {
  // 1) Read current roll (deg)
  float roll = readRollSensor();

  // 2) Compute PID output
  float setpoint = 0.0f;  // we want to hold 0° roll
  float finCmd = pidController.compute(setpoint, roll);

  // 3) Send command to actuator
  applyFinOutput(finCmd);

  // 4) Update tuner with |error|
  float absError = fabs(setpoint - roll);
  tuner.update(absError);

  // 5) Wait until next control step
  //    On ESP32 @115K baud, loop runs fast; use a small delay for ~100 Hz update:
  delay(10);
}

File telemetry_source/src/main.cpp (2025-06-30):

#include "includes.h"
#include "commandManager.h"
#include "serialManager.h"
#include "sensorManager.h"
#include "missionManager.h"

hw_timer_t *send_timer = NULL;
SerialManager xbee_serial(Serial2);
SensorManager sensor_mgr;
MissionManager mission_info;
uint8_t send_flag = 0;

void IRAM_ATTR send_1();

void setup()
{
    // Set timer to transmit at 1Hz
    send_timer = timerBegin(0, 80, true);
    timerAttachInterrupt(send_timer, &send_1, true);
    timerAlarmWrite(send_timer, 1000000, true);
    
    xbee_serial.begin();

    // Debug serial
    //Serial.begin(9600);

    // Setup SPIFF
    if(!LittleFS.begin(true))
    {
        xbee_serial.sendErrorMsg("An Error has occurred while mounting LittleFS!");
        return;
    }

    // Clean flash memory
    // nvs_flash_erase(); // erase the NVS partition
    // nvs_flash_init(); // initialize the NVS partition

    // Remove all preferences under the opened namespace
    // xbee_serial.clearPref();

    // Reset sequence
    mission_info.resetSeq(xbee_serial);

    sensor_mgr.startSensors(xbee_serial, mission_info);

    xbee_serial.sendInfoMsg("Startup Completed.");

    //Serial.println("\nStartup Completed.");
}

void loop()
{
    char cmd_buff[CMD_BUFF_SIZE];
    char send_buffer[DATA_BUFF_SIZE];
    CommandManager cmd_mgr;
    int delay_rate_ms = (1/SENSOR_SAMPLE_RATE_HZ) * 1000;
    int cannot_write_to_file = 0;
    PIDController pid_real;
    unsigned long last_servo_update = 0;

    // Run this loop at 40Hz
    while(1)
    {
        // Just process commands in idle state
        // 10Hz
        while(mission_info.getOpState() == IDLE)
        {
            if(xbee_serial.get_data(cmd_buff))
            {
                if(cmd_mgr.processCommand(cmd_buff, xbee_serial, mission_info, sensor_mgr))
                {
                    sensor_mgr.cmd_buff_to_echo(cmd_buff);
                }
            }

            vTaskDelay(pdMS_TO_TICKS(100));
        }

        xbee_serial.sendInfoMsg("MISSION STARTING!");

        sensor_mgr.resetAltData();

        if(mission_info.getOpMode() == OPMODE_SIM)
        {
            xbee_serial.sendInfoMsg("BEGIN_SIMP");
        }

        if(mission_info.getOpState() == LAUNCH_PAD && LittleFS.exists("/logs.txt")) 
        {
            xbee_serial.sendInfoMsg("Removing logs.txt from file system.");
            LittleFS.remove("/logs.txt");
        }

        File logfile = LittleFS.open("/logs.txt", FILE_APPEND);
        if(!logfile)
        {
            xbee_serial.sendErrorMsg("There was an error opening a file for saving data!");
        }

        // Start timer and camera
        digitalWrite(CAMERA1_SIGNAL_PIN, HIGH);
        digitalWrite(CAMERA2_SIGNAL_PIN, HIGH);
        timerWrite(send_timer, 0);
        timerAlarmEnable(send_timer);

        // Process command and then check for sending data
        // 40 Hz
        while(mission_info.getOpState() != IDLE)
        {
            if(xbee_serial.get_data(cmd_buff))
            {
                if(cmd_mgr.processCommand(cmd_buff, xbee_serial, mission_info, sensor_mgr))
                {
                    sensor_mgr.cmd_buff_to_echo(cmd_buff);
                }
            }

            // Wait until first simulation packet is received
            if(mission_info.getOpMode() == OPMODE_SIM && mission_info.isWaitingSimp())
            {
                vTaskDelay(pdMS_TO_TICKS(delay_rate_ms));
                continue;
            }

            sensor_mgr.sampleSensors(mission_info, xbee_serial);

            while(send_flag == 0)
            {
                /*
                if(mission_info.getOpState() == PROBE_RELEASE)
                {
                    sensor_mgr.update_imu();
                    float servo_left = 0.0;
                    float servo_right = 0.0;
                    pid_real.update_PID(sensor_mgr.getAx(), sensor_mgr.getAy(), sensor_mgr.getAz(), sensor_mgr.getGyroZ(), sensor_mgr.getMx(), sensor_mgr.getMy(), sensor_mgr.getMz(), &servo_left, &servo_right);
                    unsigned long servo_now = millis();
                    if(servo_now - last_servo_update >= 150)
                    {
                        sensor_mgr.writeGyroServoLeft(servo_left);
                        sensor_mgr.writeGyroServoRight(servo_left);
                        last_servo_update = servo_now;
                    }
                }
                */
                vTaskDelay(pdMS_TO_TICKS(25));
            }

            mission_info.incrPacketCount();
            sensor_mgr.setPacketCount(mission_info.getPacketCount());
            mission_info.beginPref("xb-set", false);
            mission_info.putPrefInt("pckts", mission_info.getPacketCount());
            mission_info.endPref();
            sensor_mgr.build_data_str(send_buffer, DATA_BUFF_SIZE);
            xbee_serial.sendTelemetry(send_buffer);
            if(logfile.size() < MAX_LOG_FILE_SIZE_BYTES)
            {
                logfile.println(send_buffer);
                //logfile.flush(); // idk
            }
            else
            {
                if(cannot_write_to_file == 0)
                {
                    xbee_serial.sendErrorMsg("Could not write to logfile, size exceeds 1MB. Data will not be written until mission is restarted.");
                }
                cannot_write_to_file = 1;
            }
            send_flag = 0;

        }

        // Back to IDLE state, turn off timer & camera, reset settings
        timerAlarmDisable(send_timer);

        int cam1_state = sensor_mgr.getCamera1Status();
        int cam2_state = sensor_mgr.getCamera2Status();

        if(cam1_state)
        {
            digitalWrite(CAMERA1_SIGNAL_PIN, LOW);
            delay(1000);
            digitalWrite(CAMERA1_SIGNAL_PIN, HIGH);
            delay(1000);
            xbee_serial.sendInfoMsg("Turning off camera 1...");
        }

        if(cam2_state)
        {
            digitalWrite(CAMERA2_SIGNAL_PIN, LOW);
            delay(1000);
            digitalWrite(CAMERA2_SIGNAL_PIN, HIGH);
            delay(1000);
            xbee_serial.sendInfoMsg("Turning off camera 2...");
        }

        mission_info.setAltCalOff();
        mission_info.waitingForSimp();
        logfile.close();
        cannot_write_to_file = 0;
    }
}

void IRAM_ATTR send_1()
{
  send_flag = 1;
} // END: send_1()

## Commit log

2024-10-05 added some sensor testing files for ardunio uno and rp0w
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2024-10-18 Added new Hall Effect Sensor schematic and created new schematic folder
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2024-10-19 Added a time calculating mechanism to detect when the magnet is first hit
2024-10-19 nour's buzzer circuit designs
    [Buzzer .kicad_pcb, Buzzer .kicad_sch]
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2024-10-26 Initial setup for hall sensor code on ESP32
2024-10-27 esp32 micropython camera documentation and stuff. need to work on camera code
2024-10-28 Add files via upload
    Re-adding sensor testing files
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2024-11-01 Revert "Renaming hall effect sensor folder names"
    This reverts commit 8cb4672ebe7f6d3157b3a361cd6c5bd58fc92823.
    [main.cpp]
2024-11-01 Added pin connections for hall effect sensor and re-organized barometer and hall effect sensor esp32 folders
2024-11-01 able to take images using esp32 cpp and save on sd card. micropython might be a dead end
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2024-11-09 Removed extra library from .ini file and addedmore print statements for the GPS data
2024-11-09 Added further time and date prints for the GPS
2024-11-09 fixed the magnetometer so that it returns stable values
    [IMU-bno085.ino]
2024-11-10 Added clarification notes to the pin connections text for the hall effect sensor
2024-11-10 Added serial print statements for no GPS position cases
2024-11-12 Added initial code for the ESP32 to write and read a log file from itself
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2024-11-16 Testing Git commands
    [Buzzer .kicad_pcb]
2024-11-16 Reverting changes
    [Buzzer .kicad_pcb]
2024-11-17 Moved new IMU code to the correct file
    [IMU_code_v2.ino]
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2024-11-25 Sketch to check for a signal on pin 21
2024-11-25 start/stop recording a MJPEG avi when a signal is received on pin 14 (needs cleaning up)
    [partitions.csv]
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2024-12-03 Added sensor data variables and implemented its functionality
2024-12-03 Helping re-organize updated IMU and motor testing files
2024-12-04 PlatformIO project
    [partitions.csv]
2024-12-06 Structured the sensor data variables into a single struct
2024-12-07 Fixed print formatting issues
    [main.cpp]
2024-12-07 Cleaned up the full sensor code and added a testing debugging code
2024-12-07 Organized ESP32 camera codes
    [partitions.csv]
2024-12-07 Removing ESP32 camera files temporarily
    [partitions.csv]
2024-12-07 Adding ESP32 camera code files back
    [partitions.csv]
2024-12-14 Emmanuel's buzzer and power management pcb updates
    [Battery.kicad_sch, Buzzer .kicad_pcb, Buzzer .kicad_sch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]
2025-01-04 simplified buzzer circuit
    [Buzzer_2.0.kicad_pcb, Buzzer_2.0.kicad_sch]
2025-01-04 Autofocus camera implementation and fixing an issue with the esp core version
    [partitions.csv]
2025-01-07 fixed buzzer circuit - removed positive net plane
    [Buzzer_2.0.kicad_pcb]
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2025-01-16 Updating RX and TX pins for the GPS module in the full sensor code
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2025-02-22 Adding inital main sensor schematic and PCB files
    [CanSat_Sensor_Board.kicad_pcb, CanSat_Sensor_Board.kicad_sch]
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2025-03-06 Adding all files including the schematics, layouts, and gerbers for the CanSat sensor and camera boards.
    [CanSat_Camera_Board-B_Cu.gbr, CanSat_Camera_Board-B_Mask.gbr, CanSat_Camera_Board-B_Paste.gbr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]
2025-03-06 Reorganizing files
    [Battery.kicad_sch, Buzzer.kicad_pcb, Buzzer.kicad_sch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]
2025-03-06 Adding STEP file models for the sensor and camera boards
    [2652 BMP280 STEMMA QT.step, 2894TR.step, 4479 LIS3MDL.step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]
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2025-03-12 Updating camera and sensor PCBs
    [CanSat_Camera_Board.kicad_pcb, CanSat_Camera_Board.kicad_sch, CanSat_Camera_Board.step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]
2025-03-12 Adding more 3D STEP models for KiCad components
    [AB38T-32.768KHZ_Cap.step, AB38T-32.768KHZ_Legs.step, SparkFun_XBee_Explorer_Regulated.step]
2025-03-15 adam's and emmanuel's updates on the power management circuit - added values for the electronics (caps, inducts...) and added buzzer EPS
    [Battery.kicad_sch]
2025-03-19 Updating new KiCad files
    [92000A013_Passivated 18-8 Stainless Steel Pan Head Phillips Screws.STEP, 971050244_M2_Standoff.step, 971050354_M3_Standoff.step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]
2025-03-22 fix camera recording logic to interperet start and stop record signals properly and refactor signaltest
    [camera-signal-test.ino]
2025-03-29 thomas checked the power circuit
    [Battery.kicad_sch]
2025-04-01 made power circuit into project and added buzzer circuit to it
    [Battery.kicad_pcb, Battery.kicad_sch]
2025-04-03 tps610333 connected PG to GND
    [Battery.kicad_sch]
2025-04-10 FSW Update: Improved state flow and processor recovery
2025-04-10 Revert "Delete sensor_testing directory"
    This reverts commit 779d1e45f94d6204a04c37606fa212a5494a937d.
    [BN-220_GPS.ino, IMU-bno085.ino, PAM3802A_-_audio_beacon.ino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]
2025-04-15 added most electrical componenets to the power circuit - missing bjt, pmos and zener for voltage proection circuit
    [Battery.kicad_sch]
2025-04-20 fixed the low voltage protection circuit after running ltspice sims
2025-04-28 Final review submission of all CanSat PCB boards and corresponding custom KiCad 3D models, footprints, and symbols
    [Battery.kicad_pcb, Battery.kicad_sch, Buzzer.kicad_pcb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]
2025-05-01 fixed stiching vias - added new logo - fixed some other vias with kc
    [CanSat_Power_Management_Board.kicad_pcb, CanSat_Sensor_Board.kicad_pcb]
2025-05-02 fixed errors and exposed copper for thermal pads
    [CanSat_Camera_Board-B_Cu.gbr, CanSat_Camera_Board-B_Mask.gbr, CanSat_Camera_Board-B_Paste.gbr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]
2025-05-03 Adding pin connections for the camera and sensor boards
2025-05-03 Refactor camera app to clean up unused features & updated config handling and GPIO definitions for recording
2025-05-08 updated pin connections for the IMU based on in person testing
2025-05-13 Fixing syntax issue in gps sensor testing file
    [main.cpp]
2025-05-13 Reorganized PCB design folder and added older versions KiCad files
    [Battery.kicad_pcb, Battery.kicad_sch, Buzzer.kicad_pcb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]
2025-05-13 Adding competition board snapshots and README to explain PCB folders
    [CanSat_Camera_Board.kicad_pcb, CanSat_Camera_Board.kicad_sch, CanSat_Power_Management_Board.kicad_pcb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]
2025-05-13 PCB improvements for the future
    [CanSat_Power_Management_Board.kicad_pcb, CanSat_Sensor_Board.kicad_pcb]
2025-05-13 Combining new BNO085 (IMU) connections to the sensor pinout text file
2025-05-23 fixed bug with csv printing
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2025-05-31 Revert "Moving RTC code into esp32_files"
    This reverts commit f19253304e994cd8ab0ea96ea5c5f37b40e2a92e.
    [main.cpp]
2025-05-31 Reverting 'beta' branch cause its stupido
    [Battery.kicad_pcb, Battery.kicad_sch, Buzzer.kicad_pcb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]
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2025-05-31 Fixed ADC calculation
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2025-06-01 Revert "Merge branch 'main' of https://github.com/adam-kabbara/RSX-CANSAT-2025 into beta"
    This reverts commit bd2a4da46b087f188f9ddec67c3be9bab7294040, reversing
    changes made to f1a6a9331ea050cb6665f4496b9fdd57a2fd9b08.
    [Battery.kicad_pcb, Battery.kicad_sch, Buzzer.kicad_pcb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]
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2025-06-02 Create pid_class.cpp
    #include "pid_class.h"
    void setup() {
    Serial.begin(115200);
    setup_servos();
    }
    void loop() {
    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
2025-06-03 Fix camera status label updates in GUI for CAMERA1 and CAMERA2
2025-06-05 fix magnetometer not reading
    [main.cpp]
2025-06-05 Revert "Merge branch 'beta' of https://github.com/adam-kabbara/RSX-CANSAT-2025 into beta"
    This reverts commit f6f80491020167b1fab35115adcb11f63c71c269, reversing
    changes made to d503fc8f721cb863899eaed8c0811128c341fa14.
    [main.cpp]
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2025-06-05 Made GPS update whenever any values are available and fixed RTC time grabbing from GPS
    [includes.h]
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2025-06-06 added map
    [cansat_data.csv]
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2025-06-06 Small fixes on camera servo code
2025-06-06 small fix for clear button
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2025-06-06 Reverting hall effect sensor logic and removing random number generator
2025-06-06 fixed max and min of camera servo
2025-06-06 Updating back to 'main'
    [Battery.kicad_pcb, Battery.kicad_sch, Buzzer.kicad_pcb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]
2025-06-06 Merging last few lost files from 'main'
    [partitions.csv]
2025-06-06 Reverting 'beta' branch code
    [includes.h, main.cpp]
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2025-06-07 rerouting release servo to fin1 jst
    [cansat_data.csv]
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2025-06-11 Added CanSat 2025 competition results and deliverables
    [3114_mission_data_cansat_2025.csv.xlsx]
2025-06-11 Isolating 'beta' branch
    [Battery.kicad_pcb, Battery.kicad_sch, Buzzer.kicad_pcb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]
2025-06-11 Revert "Merging final 2025 competition code"
    [Battery.kicad_pcb, Battery.kicad_sch, Buzzer.kicad_pcb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]
2025-06-11 Adding back telemetry_source and ground_station_source directories
    [cansat_data.csv]
2025-09-12 Adding 2T6 potential PCB improvment work
    [Power_Isolation_Example.kicad_pcb, Power_Isolation_Example.kicad_sch]
